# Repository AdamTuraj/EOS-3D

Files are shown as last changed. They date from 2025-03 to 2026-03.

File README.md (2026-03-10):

<center><h1>EOS 3D</h1>

**A cheap cantilever 3D printer with full self calibration capabilities.**

This printer was made for the [Hackclub](http://hackclub.com) "Infill" event.

</center>

## Goal

- $300 (USD) budget
- Klipper compatibility
- No calibration printing is required
- 180x180mm build space
- Cantilever structure
- CFD-optimized part cooling
- Safety considerations:
  - Must not pose a fire hazard
  - Must not cause harm to the user
- ~~[PicoMMU](https://github.com/lhndo/LH-Stinger/tree/main/User_Mods/MMU/Stinger%20Pico%20MMU%20-%20%40LH) compatibility~~

## The Result

After a complete redesign, flaws from early part choices created major issues in the final build. These challenges taught me valuable lessons for future projects, especially regarding keeping structures stiff, following good design practices to avoid pitfalls, and approaching wiring more thoughtfully.

As of writing this README, the printer is about 80% complete but still far below my minimum standards. The main reasons are:

- Wiring: In V1, I cut the wires too short (even for that build they were barely long enough). With V2, they simply couldn’t reach.
- Rigidity: The Z and X axes weren’t stiff enough. This was the biggest issue—I underestimated the limitations of ASA and couldn’t reinforce it enough to minimize flex.
- X-axis rods: These should have been slightly longer to give the XZ mount more gripping surface.
- Lack of time: With university starting in a few days, I do not have enough time to finish it.

It was painful to call this project off, but it has been an invaluable learning experience. From V1 to V2, I made many improvements (and some regressions) to the design. The toolhead was by far the biggest success. With a larger budget, I’d rebuild the machine entirely from the ground up; however, that will be for the future

Below are images of the printer:

EOS V2:
EOS V2

EOS V1:
EOS V1

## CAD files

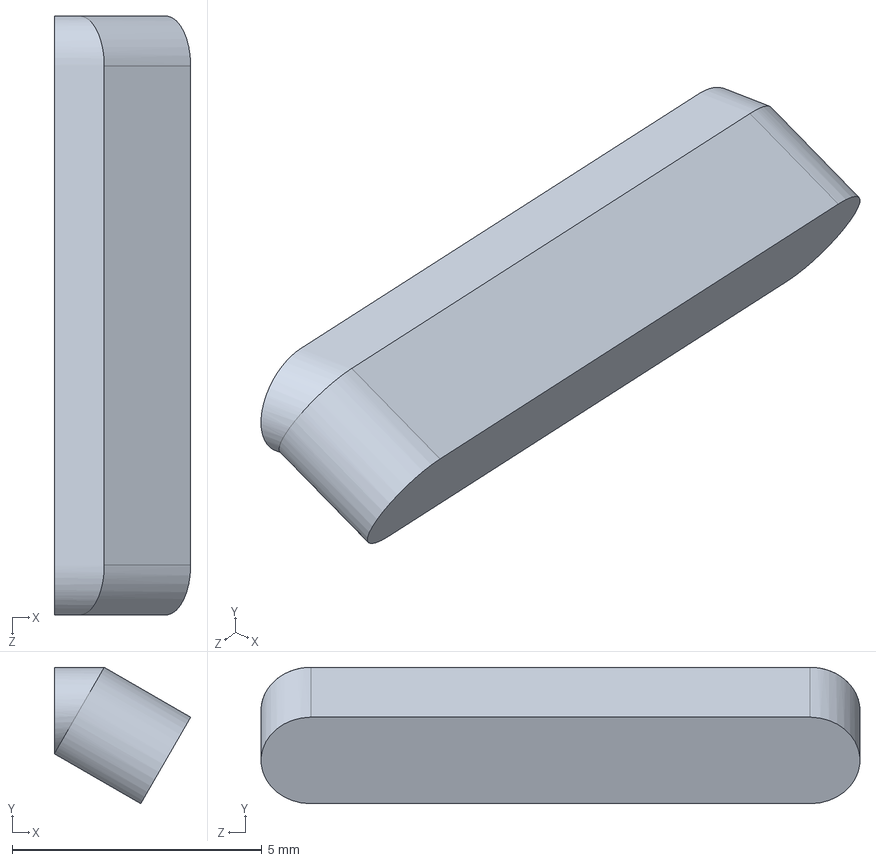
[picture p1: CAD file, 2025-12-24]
Toolhead/Fan Shroud.SLDPRT
2.73 x 2.73 x 12.0 mm

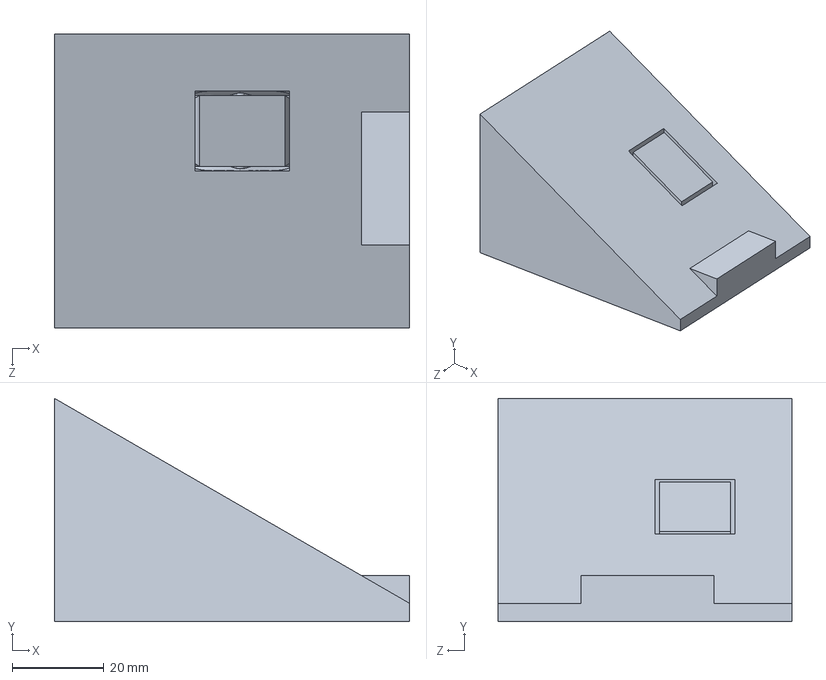
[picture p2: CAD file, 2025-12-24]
Toolhead/CFD Tool.SLDPRT
77.2 x 48.6 x 64.0 mm

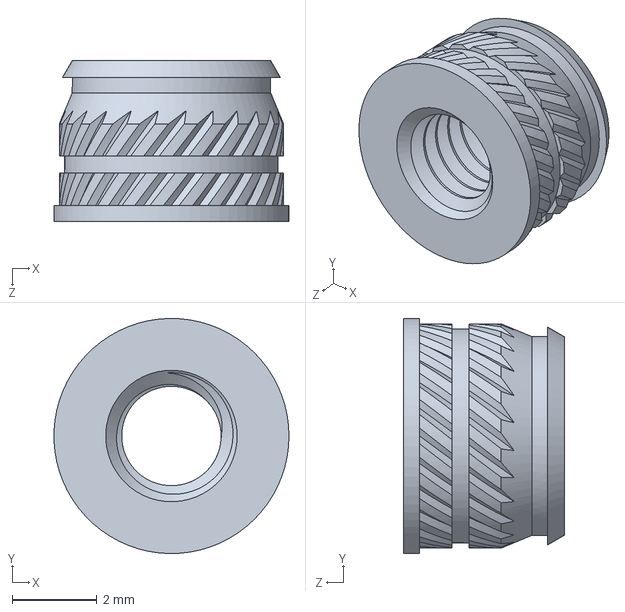
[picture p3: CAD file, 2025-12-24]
Vendor Hardware/M3x4mm Heat-Set Insert.SLDPRT
5.56 x 5.56 x 3.80 mm

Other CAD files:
Toolhead/E3D_V6.SLDASM
Toolhead/5015 Blower Fan.SLDPRT
Toolhead/Fan Cover.SLDPRT
Toolhead/3010 Radial Fan.SLDPRT
Toolhead/Hotend Mount.SLDPRT

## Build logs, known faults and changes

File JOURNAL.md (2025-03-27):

<center><h1>EOS 3D</h1></center>

**This document tracks progress for the YSWS portion of this project. It also serves as a journal documenting the development process.**

## Preface

Before starting this project, I must outline the key requirements to ensure clear project direction and successful execution. I initially came up with the following requirements:

- $300 (USD) budget
- Klipper compatibility
- No calibration printing is required
- 180x180mm build space
- Cantilever structure
- CFD-optimized part cooling
- Safety considerations:
  - Must not pose a fire hazard
  - Must not cause harm to the user
- [PicoMMU](https://github.com/lhndo/LH-Stinger/tree/main/User_Mods/MMU/Stinger%20Pico%20MMU%20-%20%40LH) compatibility

Although I have extensive experience working with 3D printers, this is my first time designing one. Through this process, I aim to deepen my understanding of 3D printer mechanics, refine my CAD skills, and improve my approach to mechanical design. Additionally, thanks to Hack Club, this project offers the added benefit of a free printer.

The name of this project, **EOS 3D**, is inspired by the Greek goddess of dawn, Eos. Dawn symbolizes new beginnings, reflecting a personal milestone in my projects and an entry point for tinkerers.

## Day 1 (February 1st, 2025)

Hours worked: **8**

Total hours on project: **8**

### BOM Selection

Creating the **Bill of Materials (BOM)** required balancing cost-effectiveness with performance and safety. While selecting parts, I took into account the following:

- A budget hotend from a reputable brand to ensure safety and good flow.
- A reliable direct-drive extruder.
- The **Cartographer probe** for its high-resolution bed meshing capabilities and automatic Z-offset calibration via Carto Survey.
- BTT SKR Mini and a Raspberry PI for its cost-effective control.
- A cheap heated bed with a PEI spring steel sheet.
- A PSU with a large overhead from a reputable brand.

Compiling and refining the BOM took approximately **four hours**.

**[BOM Link](https://docs.google.com/spreadsheets/d/1bcc6GYku32MK7iQRG4SbK_M0EsOTyS6UKOEk-3bwc5s)**

### Toolhead Development

With the BOM completed, I decided to tackle the printer's tool head first, as it serves as an "anchor point" for the build.

I began by modelling the X-axis rods and bearings to establish clearance constraints between the toolhead and the rods.

Next, I imported the CAD models for the Sherpa Mini extruder and the E3D V6 hotend, then started designing a mounting solution. I opted for a clamping mechanism for the hotend, as shown in the image below:

Hotend clamping mechanism

By the end of the day, I refined the mounting system and securely integrated the Sherpa Mini with the mount. Below is the final design on day 1 (ignore the mesh issues on the Sherpa; those were present in the CAD model):

Day 1 image update

## Day 2 (February 2nd, 2025)

Hours worked: **2**

Total hours on project: **10**

### Further Toolhead Development

Today, I completed the connection of the toolhead to the linear bearings with inspiration from the Prusa Mini. I began modeling the cooling fan duct but encountered challenges in designing one that is both functional and aesthetically pleasing.

Here is the final model of the day:
Day 2 image update

## Day 3 (February 3rd, 2025)

Hours worked: **1**

Total hours on project: **11**

### Fan Development

Today, I did minimal work; however, I finished and placed the part cooling fan. Tomorrow, I will begin designing it and running CFD tests.

Day 3 image update

## Day 4 & 5 (February 5th-6th, 2025)

Hours worked: **4**

Total hours on project: **15**

### First Fan Iteration Completed

After extensive trial and error, I have an initial design for the fan duct. The goal was to implement a dual exhaust setup, which presents more challenges but should enable more even cooling across the print.

Next Steps Before CFD Analysis:

- Raise the outlets so they are positioned above the nozzle.
- Adjust the outlet angles to prevent airflow from hitting the nozzle.
- Increase clearance to the hotend to prevent outlet deformation

With these changes, I plan to start optimizing the design tomorrow before running CFD simulations. Below are images of the fan duct (rear view) and the complete model in its current form.

Fan duct from the rear

Day 4 & 5 image update

## Day 6 (February 7th, 2025)

Hours worked: **5**

Total hours on project: **20**

### Computational Fluid Dynamics

With the latest changes in place, it was finally time to put the design through CFD analysis. Having never used CFD software before, I knew this would be a challenging process.

I initially tried Autodesk CFD and ANSYS Workbench, but getting them to work felt overwhelming. Eventually, I discovered SimScale, which turned out to super user-friendly. I followed [this YouTube tutorial](https://www.youtube.com/watch?v=1pMJQetyA4A) to set everything up.

After a long computation wait, I finally got to see the airflow results—and they were really bad. Not entirely surprising for an initial design, but definitely something to improve. The results are shown below:

CFD Results

Tomorrow, I’ll begin optimizing the design and rerun the CFD analysis to see how much improvement can be made.

Day 6 image update

## Day 7 (February 8th, 2025)

Hours worked: **6**

Total hours on project: **26**

### Finishing the Part Cooling Duct

After reflecting on yesterday’s analysis, I decided to try a different ducting style to improve overall airflow. This new design features a 180° duct, which I hoped would distribute air more evenly. I started by sketching the outlet, connecting it to the rest of the duct, and running it through CFD. After setting everything up, I obtained the following result:

### CFD Run 1

CFD Result #1 Top  
CFD Result #1 Bottom

As shown in the results, the airflow was heavily biased to the left, causing a lack of airflow through the right slit and the exit airflow being angled.

For the next iteration, I attempted to make the turn more gradual to prevent the airflow from favoring the left.

### CFD Run 2

CFD Result #2 Top  
CFD Result #2 Bottom

The results looked good! However, there were still three issues:

- The airflow was still left-biased.
- There was a lot of extra space (look at the top left and bottom right of the ducts).
- **There was no airflow through the rightmost duct when there was no object "printing," as shown below. This is the big one.**

CFD Result #2 Top No object

For the next run, I made some adjustments to the ducting to make it more smooth and prevent the sharp corner. I also made the throat leading up to the outlet smaller and added a fillet to the outermost outlets.

### CFD Run 3

CFD Result #3 Top  
CFD Result #3 Bottom

With the throat being tighter, I was hoping for the air to be forced into the right side; however, this was not the case.

I then made the interior of the outlet slightly smaller horizontally so there was less open space and made some adjustments to the ducting leading up to the outlet.

### CFD Run 4

CFD Result #4 Top  
CFD Result #4 Bottom

These changes were a big step forward in resolving the overall bias issue. There was still some airflow lacking on the right side; however, the airflow was less skewed.

For the next run, I added a barrier down the middle to help balance the airflow between the two halves.

### CFD Run 5

CFD Result #5 Top  
CFD Result #5 Bottom

Adding the barrier finally solved the issue, and there is really nice flow. It pretty much goes straight down the middle, and each slit is getting sufficient airflow. I decided this was good enough and moved on.

The only thing I would really change is the angle of the slits, but this design is sufficient and looks nicer.

### Post CFD

With the part cooling fan optimized, I quickly designed a mount for everything and called it a night.

### Note

Before I end this journal entry, I want to mention that I did use AI (specifically ChatGPT) to assist me in optimizing the design. I have no formal education in this space and no mentors to help me out, so using AI was my best bet.

Tomorrow, I will be finishing off the toolhead with the mount for the Cartographer and PicoMMU "Hub."

Day 7 Image Update

## Day 8 (February 10th, 2025)

Hours worked: **2**

Total hours on project: **28**

### Finishing the toolhead

Today, I modified the part cooling fan mount to improve its aesthetics and structural integrity. I also installed the Cartographer probe using a simple mount. Tomorrow, I will begin working on the X-axis!

Note: The PicoMMU infrastructure will be added after the initial prototype is completed.

Day 8 Image Update

## Day 9, 10, & 11 (February 11th-13th)

Hours worked: **5**

Total hours on project: **33**

### Begin the X axis

Over the past few days, I implemented the belting for the X-axis using a clamping system that secures the belt with a screw. The endplate design is based on the Prusa Mini, as it was the simplest solution after testing other strategies.

Day 9 Image Update

# Day 12 & 13 (February 14th-15th)

Hours worked: **2**

Total hours on project: **35**

### Z Axis Work

I have been working on the mounts and positioning of the Z-axis. Due to the simplicity of the design, not much work was required.

Day 12 Image Update

# Day 14, 15, 16 (February 16th-19th)

Hours worked: **5**

Total hours on project: **40**

### Finish Z Axis

Over day 14, 15, and the start of day 16, I finished the Z axis. This means I will be starting the last axis of the project, the Y axis.

### Start Y Axis

On day 16, I started the Y axis. As of now, I have the extrusion, rails, and carriage designed. The carriage will be 3D printed with the [CarbonX PA12-CF](https://www.3dxtech.com/products/carbonx-nylon-12-cf-1). It is an expensive filament; however, it has a very high Tg (150°C) compared to Bambulab PAHT-CF and Polymaker's counterpart (both are around 70°C).

Tomorrow, I will design the endplates for the rails and extrusion, the mount holding the carriage to the bearings, and the belting.

Other than that, I just have to design the mounts for the electronics (motherboard, RPi, and power supply), and I'm done!

Day 16 Image Update

# Day 17, 18 (February 20th-21st)

Hours worked: **6**

Total hours on project: **46**

### Finish the printer!

I have been slacking a little bit on the journal while finishing the printer off. Anyways, its done! I don't have much to say but it was just a lot of fitting things together and basic problem solving. I will be revising the BOM tomorrow to add some things that have changed.

Soon, I will order the parts, print the printed parts and start building!

Day 18 Image Update

# Day 19, 20 (February 23rd-24th)

Hours worked: **3**

Total hours on project: **49**

### Ordering the Parts

With the printer completed, I successfully received my grant! Before placing orders, I had to swap out several parts due to availability issues. I then ordered the Carto probe and Raspberry Pi Zero from their respective websites. However, I encountered payment issues on AliExpress, as my card was being declined. After several attempts and troubleshooting, I finally managed to place the order successfully. Now, all that's left is to wait for the parts to arrive and finish printing all the necessary components!

### Colouring the Printed Parts

I want my printer to be black with green accents, so I painted some selected parts green for contrast. Additionally, I created a 3MF file to easily reproduce the design in the future.

**The images for this day were lost :(**

# Day 21, 22, 23 (March 7th-9th)

Hours worked: **10**

Total hours on project: **59**

### Parts came in!

I have received all but one part. This means I can get building! Before printing, I tested all the electronic parts to make sure they were working. Luckily they all were working as advertised so I began printing!

### PSU Changes

Before printing, I realized the PSU was much bigger than the CAD model I initially chose. Therefore, I had to make some changes to the bumper to compensate for this change.

### Hotend Changes

I made some slight changes to some of the hotend assembly to improve printability and a few fixes.

I'm hoping to be able to start building everything tomorrow morning!

### TODO

- Add back all the fasteners lost with the changes

Day 23 Image Update

# Day 24, 25 (March 21st-22nd)

Hours worked: **6**

Total hours on project: **65**

### Making adjustments

After the initial printing of the parts, I had to make adjustments for fitment, among other issues. These included adjusting the PSU mounts, adjusting the mounting to aluminum extrusions (I thought they had screw holes threaded) and the part cooling fan.

#### Part cooling fan

The old design was not fitting well due to a screw on the heatblock I did not account for. Instead of struggling to change it, I decided to completly redesign the part cooling fan duct. It now uses a single flat nozzle. After running CFD, the airflow is just as good as the original design with the added bonus of being a lot less complicated. Below is the CFD analysis and the duct itself:

New part cooling duct
CFD Results redesign side view
CFD Results redesign top view

### Final remarks

Firstly, I just want to give an update on why there was a two week break. I was on vacation and could not work on the project. Secondly, I plan on adding the PicoMMU integration (really just a filament cutter and mount for the 4-1 bowden hub) once I have the printer up and running. I still have to add back all the fasteners. Its a PITA to do and I plan on doing it all in one go once the design in finalized.

Day 25 Image Update

# Day 26, 27, 28 (March 24th-27th)

Hours worked: **5**

Total hours on project: **70**

### X-axis Issues

After assembling the X-axis, I noticed that it could twist, which is obviously not ideal. Despite strengthening the area and tightening the rod fitment, the problem persisted. It wasn’t until I discovered that the rods were not fully inserted that I was able to resolve the issue.

### Final Assembly

I made a few minor modifications to some components, and the axis is finally complete! Below is an overview of the physical build:

XZ axis build

Day 28 Image Update

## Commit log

2025-02-11 Day 8. Toolhead is done!!!
2025-12-24 Begin v3 redesign. Add hotend mount and part cooling duct
    [3010 Radial Fan.SLDPRT, 5015 Blower Fan.SLDPRT, CFD Tool.SLDPRT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]
2026-03-10 Replace printer images in README
    Updated images for EOS V1 and EOS V2 in README.
2026-03-10 Update README with EOS V2 printer image
    Added image of EOS V2 printer to README.
